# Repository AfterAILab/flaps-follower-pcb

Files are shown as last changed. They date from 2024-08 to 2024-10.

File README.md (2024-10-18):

# AfterAI Flaps Follower PCB

This repository is part of the [AfterAI Flaps](https://afterai.dev/flaps) project.
You can purchase AfterAI Flaps goods at [AfterAI's online store](https://shop.afterai.dev). 

## How to Order a PCB

You can order a PCB from [JLCPCB](https://jlcpcb.com).
You need to create a gerber file from the KiCad project. You can use the [Fabrication Toolkit](https://github.com/afterai-dev/flaps-fabrication-toolkit) to create the gerber file.
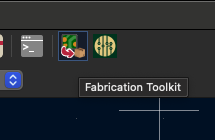
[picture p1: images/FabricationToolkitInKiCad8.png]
Fabrication toolkit in Kicad8


## Software Repository

- [flaps-avr](https://github.com/AfterAILab/flaps-avr) - Firmware for the AVR microcontroller

## How to Upload Program to the PCB

https://afterai.dev/Zettelkasten/How+to+Upload+Program+to+AfterAI+Flaps+Follower

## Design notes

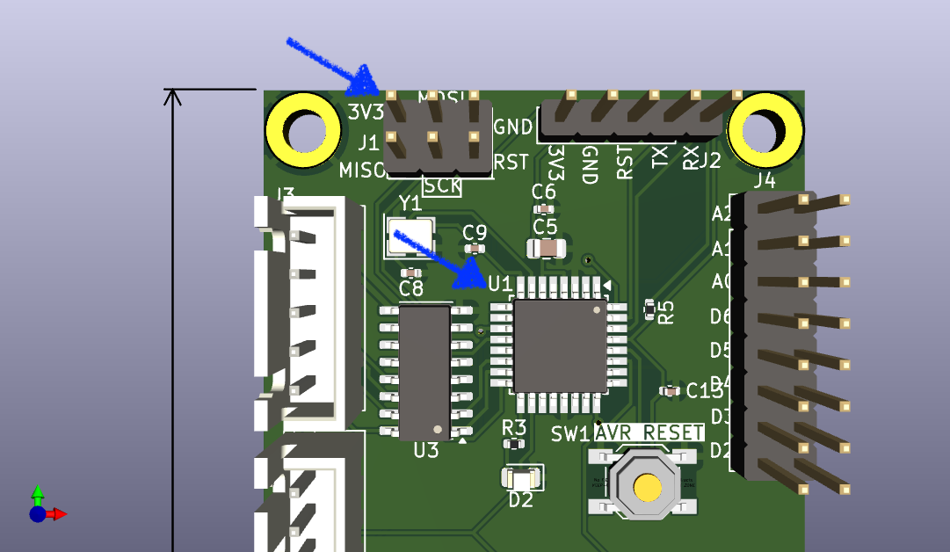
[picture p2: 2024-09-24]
images/Follower-U1-Peripherals.png

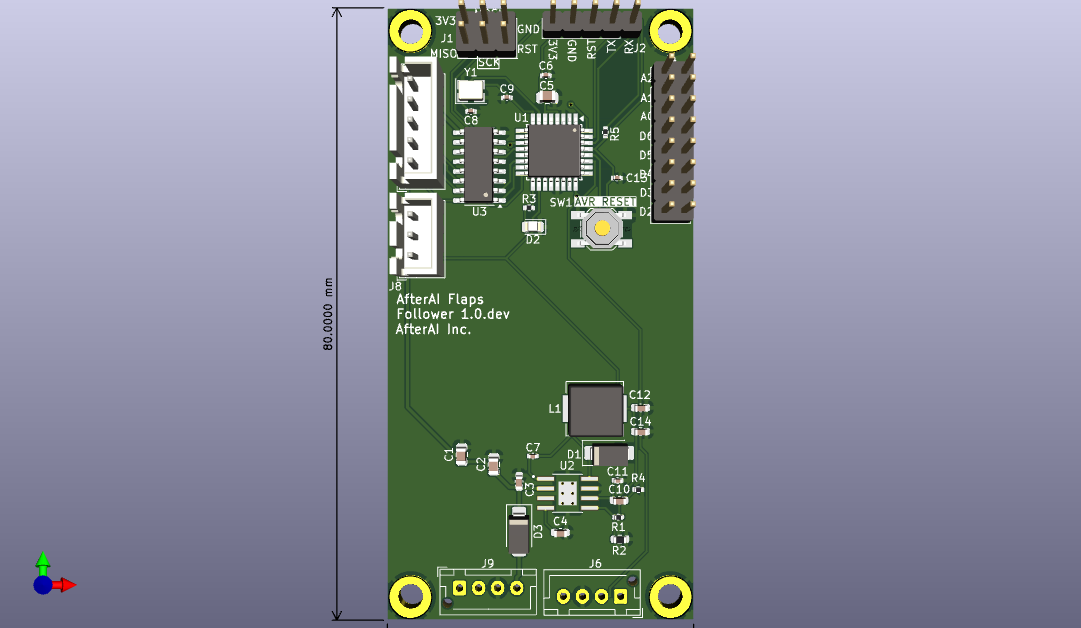
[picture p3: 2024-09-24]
images/Follower.png

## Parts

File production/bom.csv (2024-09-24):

Designator | Footprint | Quantity | Value | LCSC Part #
C1, C2 | 0805 | 2 | 4.7u | C77077
C10 | 0603 | 1 | 1nF | C1636
C11 | 0402 | 1 | 47pF | C60137
C12, C14 | 0603 | 2 | 47u | C140782
C13, C6, C7 | 0402 | 3 | 0.1u | C307331
C3, C4 | 0603 | 2 | 0.01u | C77053
C5 | 0805 | 1 | 10uF | C440198
C8, C9 | 0402 | 2 | 22pF | C1555
D1, D3 | D_SMA | 2 | B340A | C3018525
D2 | 0805 | 1 | LED | C2297
J1 | PinHeader_2x03_P2.54mm_Vertical | 1 | AVR-ISP-6 | C65114
J2 | PinHeader_1x05_P2.54mm_Vertical | 1 | Serial-328P | C492404
J3 | JST_XH_B5B-XH-AM_1x05_P2.50mm_Vertical | 1 | Conn_01x05_Pin | C161872
J4 | PinHeader_2x08_P2.54mm_Vertical | 1 | Conn_02x08_Odd_Even | C5383108
J6, J9 | JST_XH_B4B-XH-AM_1x04_P2.50mm_Vertical | 2 | Conn_01x04_Pin | C161871
J8 | JST_XH_B3B-XH-AM_1x03_P2.50mm_Vertical | 1 | HallSensor | C161870
L1 | L_Sunlord_MWSA0603S | 1 | 6.8uH | C408449
R1 | 0402 | 1 | 10.2k | C11660
R2 | 0603 | 1 | 3.24k | C22994
R3 | 0402 | 1 | 120 | C25079
R4 | 0402 | 1 | 29.4k | C327356
R5 | 0402 | 1 | 10k | C25744
SW1 | SW_SPST_SKQG_WithStem | 1 | RESET | C318884
U1 | TQFP-32_7x7mm_P0.8mm | 1 | ATmega328P-A | C14877
U2 | CONV_TPS54331DDAR | 1 | TPS54331DDAR | C90761
U3 | SOIC-16_3.9x9.9mm_P1.27mm | 1 | ULN2003A | C7512
Y1 | Crystal_SMD_3225-4Pin_3.2x2.5mm | 1 | 16MHz | C13738

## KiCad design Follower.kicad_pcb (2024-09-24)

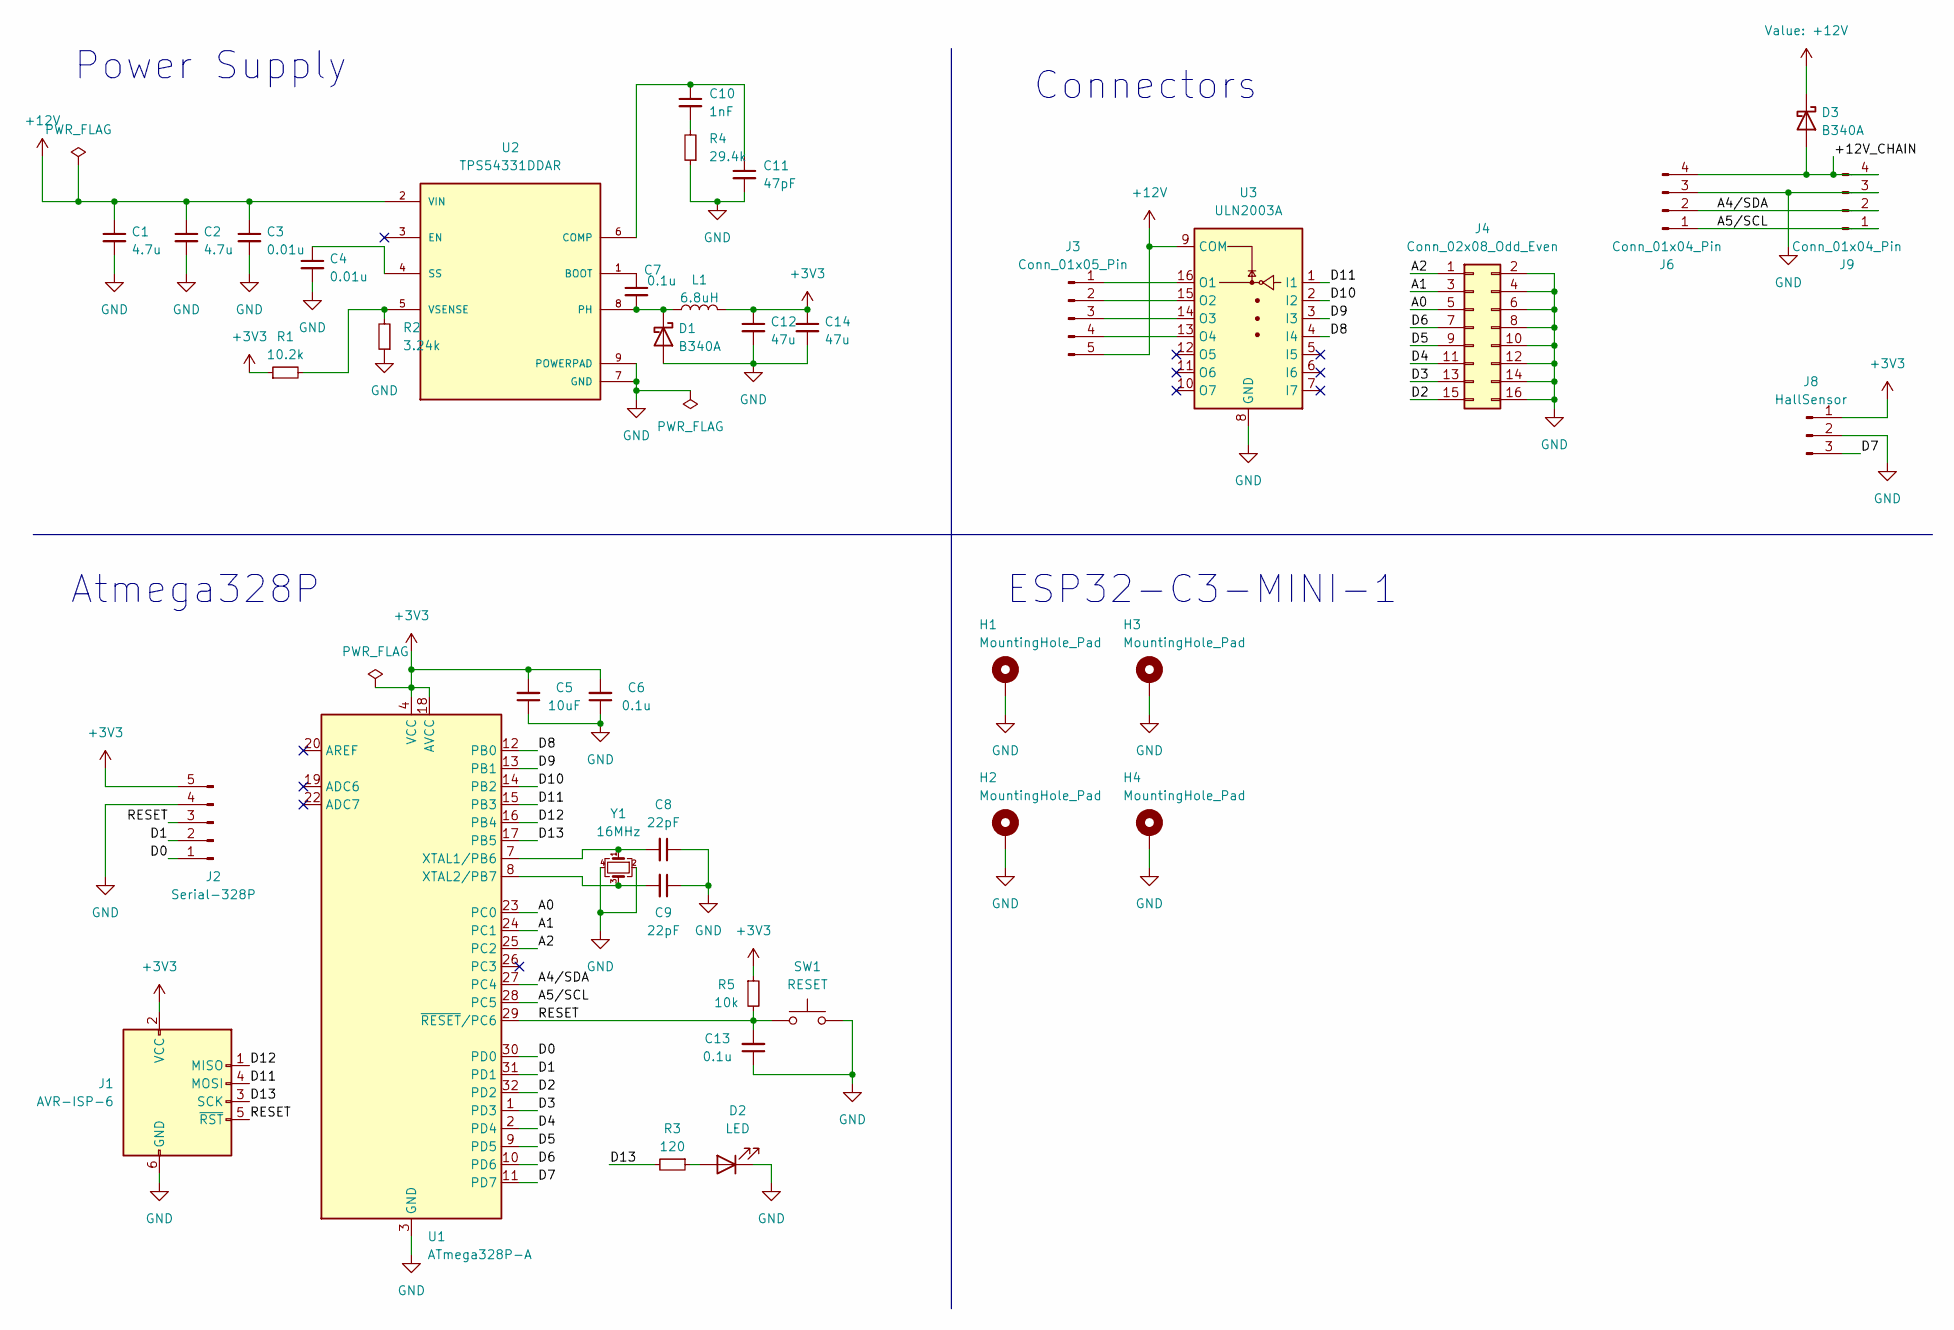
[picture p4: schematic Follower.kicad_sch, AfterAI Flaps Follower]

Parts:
C1, C2: 4.7u; C_0805_2012Metric; LCSC C77077
C3, C4: 0.01u; C_0603_1608Metric; LCSC C77053
C5: 10uF; C_0805_2012Metric; LCSC C440198
C6, C7, C13: 0.1u; C_0402_1005Metric; LCSC C307331
C8, C9: 22pF; C_0402_1005Metric; LCSC C1555
C10: 1nF; C_0603_1608Metric; LCSC C1636
C11: 47pF; C_0402_1005Metric; LCSC C60137
C12, C14: 47u; C_0603_1608Metric; LCSC C140782
D1, D3: B340A; D_SMA; LCSC C3018525
D2: LED; LED_0805_2012Metric; LCSC C2297
H1, H2, H3, H4: MountingHole_Pad; MountingHole_3.2mm_M3_DIN965_Pad
J1: AVR-ISP-6; PinHeader_2x03_P2.54mm_Vertical; LCSC C65114
J2: Serial-328P; PinHeader_1x05_P2.54mm_Vertical; LCSC C492404
J3: Conn_01x05_Pin; JST_XH_B5B-XH-AM_1x05_P2.50mm_Vertical; LCSC C161872
J4: Conn_02x08_Odd_Even; PinHeader_2x08_P2.54mm_Vertical; LCSC C5383108
J6, J9: Conn_01x04_Pin; JST_XH_B4B-XH-AM_1x04_P2.50mm_Vertical; LCSC C161871
J8: HallSensor; JST_XH_B3B-XH-AM_1x03_P2.50mm_Vertical; LCSC C161870
L1: 6.8uH; L_Sunlord_MWSA0603S; LCSC C408449
R1: 10.2k; R_0402_1005Metric; LCSC C11660
R2: 3.24k; R_0603_1608Metric; LCSC C22994
R3: 120; R_0402_1005Metric; LCSC C25079
R4: 29.4k; R_0402_1005Metric; LCSC C327356
R5: 10k; R_0402_1005Metric; LCSC C25744
SW1: RESET; SW_SPST_SKQG_WithStem; LCSC C318884
U1: ATmega328P-A; TQFP-32_7x7mm_P0.8mm; LCSC C14877
U2: TPS54331DDAR; CONV_TPS54331DDAR; PARTREV F; LCSC C90761
U3: ULN2003A; SOIC-16_3.9x9.9mm_P1.27mm; LCSC C7512
Y1: 16MHz; Crystal_SMD_3225-4Pin_3.2x2.5mm; LCSC C13738

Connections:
+3V3: C5.2, C6.2, C12.1, C14.1, J1.2 (VCC), J2.5, J8.1, L1.2, R1.1, R5.1, U1.4 (VCC), U1.6 (VCC), U1.18 (AVCC)
+12V: C1.1, C2.1, C3.1, D3.1 (K), J3.5, U2.2 (VIN), U3.9 (COM)
/+12V_CHAIN: D3.2 (A), J6.4, J9.4
/A0: J4.5, U1.23 (PC0)
/A1: J4.3, U1.24 (PC1)
/A2: J4.1, U1.25 (PC2)
/A4/SDA: J6.2, J9.2, U1.27 (PC4)
/A5/SCL: J6.1, J9.1, U1.28 (PC5)
/D0: J2.1, U1.30 (PD0)
/D1: J2.2, U1.31 (PD1)
/D2: J4.15, U1.32 (PD2)
/D3: J4.13, U1.1 (PD3)
/D4: J4.11, U1.2 (PD4)
/D5: J4.9, U1.9 (PD5)
/D6: J4.7, U1.10 (PD6)
/D7: J8.3, U1.11 (PD7)
/D8: U1.12 (PB0), U3.4 (I4)
/D9: U1.13 (PB1), U3.3 (I3)
/D10: U1.14 (PB2), U3.2 (I2)
/D11: J1.4 (MOSI), U1.15 (PB3), U3.1 (I1)
/D12: J1.1 (MISO), U1.16 (PB4)
/D13: J1.3 (SCK), R3.2, U1.17 (PB5)
/RESET: C13.2, J1.5 (~RST), J2.3, R5.2, SW1.1, U1.29 (~RESET/PC6)
GND: C1.2, C2.2, C3.2, C4.2, C5.1, C6.1, C8.1, C9.1, C11.2, C12.2, C13.1, C14.2, D1.2 (A), D2.1 (K), H1.1, H2.1, H3.1, H4.1, J1.6 (GND), J2.4, J4.2, J4.4, J4.6, J4.8, J4.10, J4.12, J4.14, J4.16, J6.3, J8.2, J9.3, R2.1, R4.1, SW1.2, U1.3 (GND), U1.5 (GND), U1.21 (GND), U2.7 (GND), U2.9 (POWERPAD), U3.8 (GND), Y1.2, Y1.4
unnamed: C10.2, R4.2
unnamed: C7.2, D1.1 (K), L1.1, U2.8 (PH)
unnamed: D2.2 (A), R3.1
unnamed: J3.1, U3.16 (O1)
unnamed: J3.2, U3.15 (O2)
unnamed: J3.3, U3.14 (O3)
unnamed: J3.4, U3.13 (O4)
unnamed: C8.2, U1.7 (XTAL1/PB6), Y1.1
unnamed: C9.2, U1.8 (XTAL2/PB7), Y1.3
unnamed: C7.1, U2.1 (BOOT)
unnamed: C10.1, C11.1, U2.6 (COMP)
unnamed: C4.1, U2.4 (SS)
unnamed: R1.2, R2.2, U2.5 (VSENSE)

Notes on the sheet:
Connectors
Power Supply
ESP32-C3-MINI-1
Atmega328P

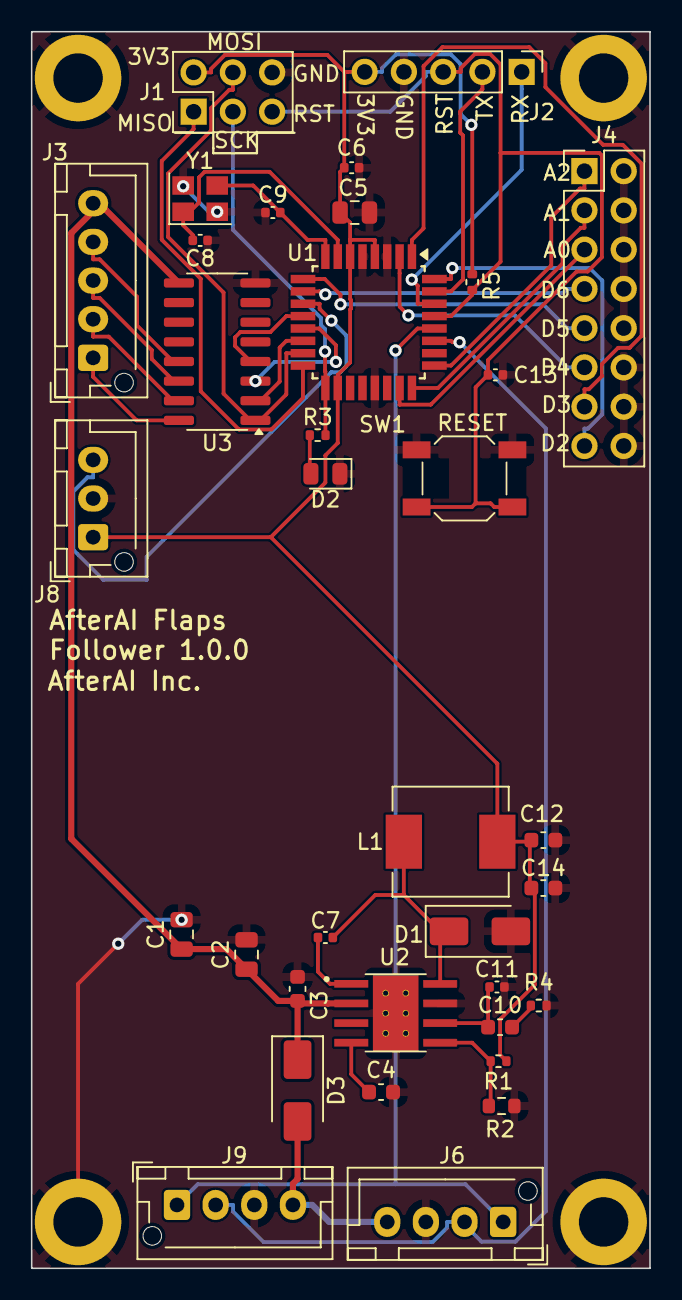
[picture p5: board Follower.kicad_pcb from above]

Board: 2 copper layers, 40.0 x 80.0 mm, 39 parts (0 on the bottom side), 37 nets.
